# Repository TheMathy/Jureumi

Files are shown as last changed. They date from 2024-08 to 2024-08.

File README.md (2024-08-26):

# Jureumi

Jureumi is a maze-solving robot built by **Mathias Suroviak**, **Lucia Hutirová** and **Lucia Eliška Grajciarová**. He was built as our [SOČ](https://siov.sk/sutaze/stredoskolska-odborna-cinnost/) project and to attend the [Micromouse](https://en.wikipedia.org/wiki/Micromouse) competition.

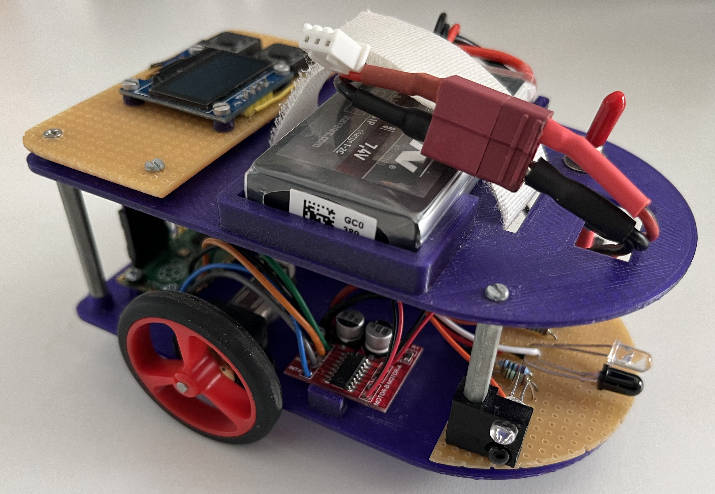
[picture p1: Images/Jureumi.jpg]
SideTop Render of Jureumi


***

## Features
Although Jureumi is relatively simple in compare with other Micromouse robots, he contains all the necessary features to solve mazes:
- Drive through the maze using two brushed DC motors
- Detect obstacles - maze walls with custom made IR distance sensors
- Scan mazes, where all walls are connected, using [Right-hand rule](https://en.wikipedia.org/wiki/Maze-solving_algorithm#Hand_On_Wall_Rule)
- Save map of the maze to raspberry pi pico flash memory

***

## Components

| Component | Model | Quantity |
| --- | --- | --- |
| Microcontroller | [Raspberry Pi Pico](https://www.raspberrypi.com/products/raspberry-pi-pico/) | 1 |
| Linear Regulator | LM317 Module | 1 |
| Motor | [Pololu 75:1 Gearmotor HP](https://www.pololu.com/product/2215) | 2 |
| Encoder | [Pololu Encoder 12 CPR](https://www.pololu.com/product/4761)| 2 |
| Wheel | [Pololu WHEEL 40×7MM - RED](https://www.pololu.com/product/1453) | 2 |
| Motor Driver | MX1508 Module | 1 |
| Ball Caster | [Pololu Ball Caster - 3/8″ Metal Ball](https://www.pololu.com/product/951) | 1 |
| IR LED | LL-503IRC2V-2AD | 3 |
| Phototransistor | BPV11F | 3 |
| Display | SSD-1306 OLED display | 1 |
| Battery | KAVAN Li-Po 350mAh/7,4V | 1 |

***

## Future improvements:
- More reliable distance sensors (sunlight cover, smaller detection angle, smaller light frequency range, ...)
- Advanced maze-solving algorithms (A*, Floodfill)
- Custom PCB including MCU
- Replace the linear voltage regulator with a buck converter

***

## Images
### Renders

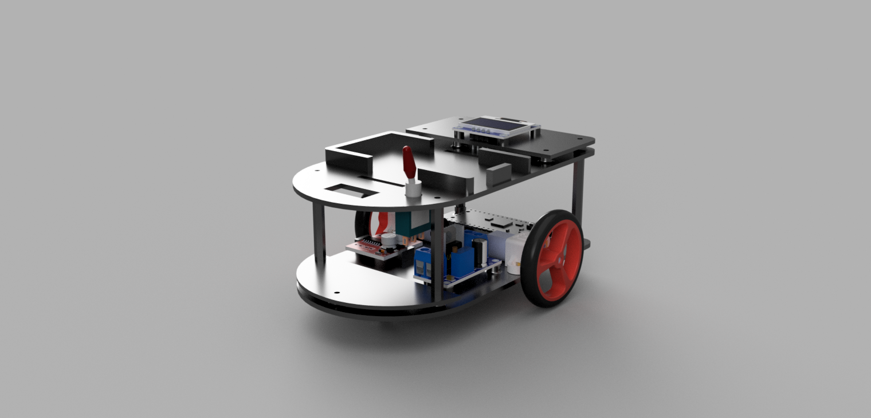
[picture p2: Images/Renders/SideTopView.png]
SideTop View Render of Jureumi

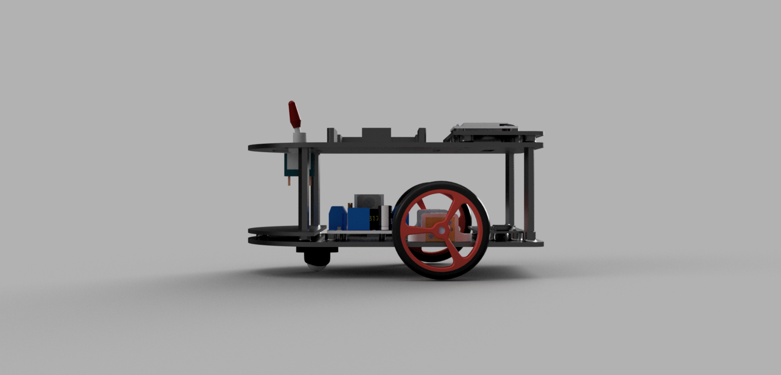
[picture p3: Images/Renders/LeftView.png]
Left View Render of Jureumi


### Visualized maze-map from robot's memory
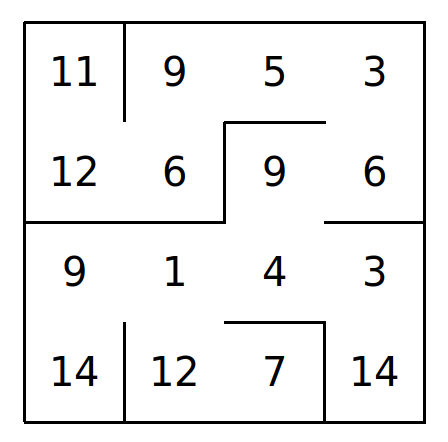
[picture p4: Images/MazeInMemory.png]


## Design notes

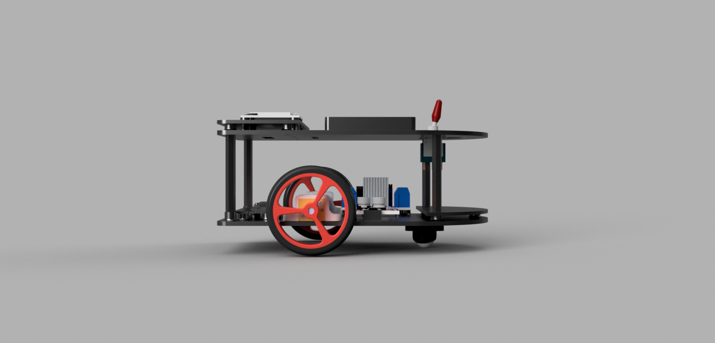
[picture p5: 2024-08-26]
Images/Renders/RightView.png

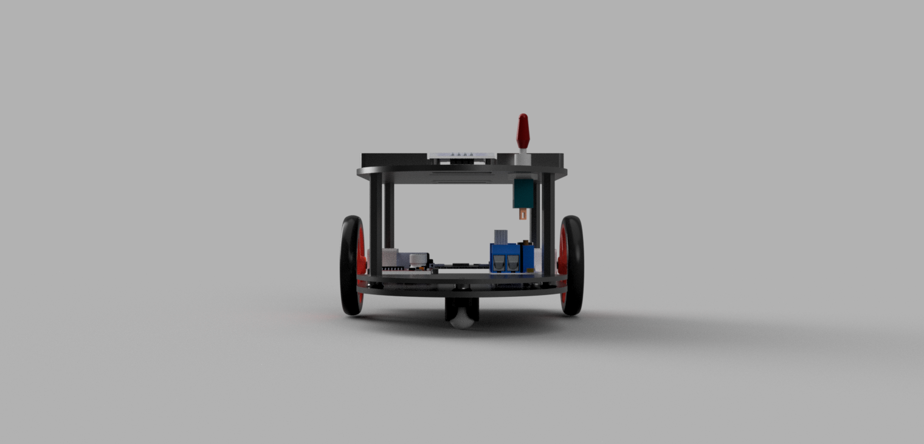
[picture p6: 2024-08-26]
Images/Renders/FrontView.png

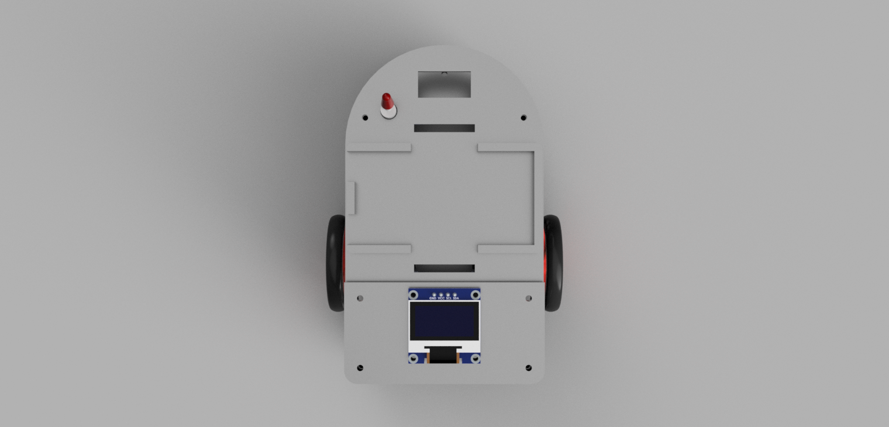
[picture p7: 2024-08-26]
Images/Renders/TopView.png

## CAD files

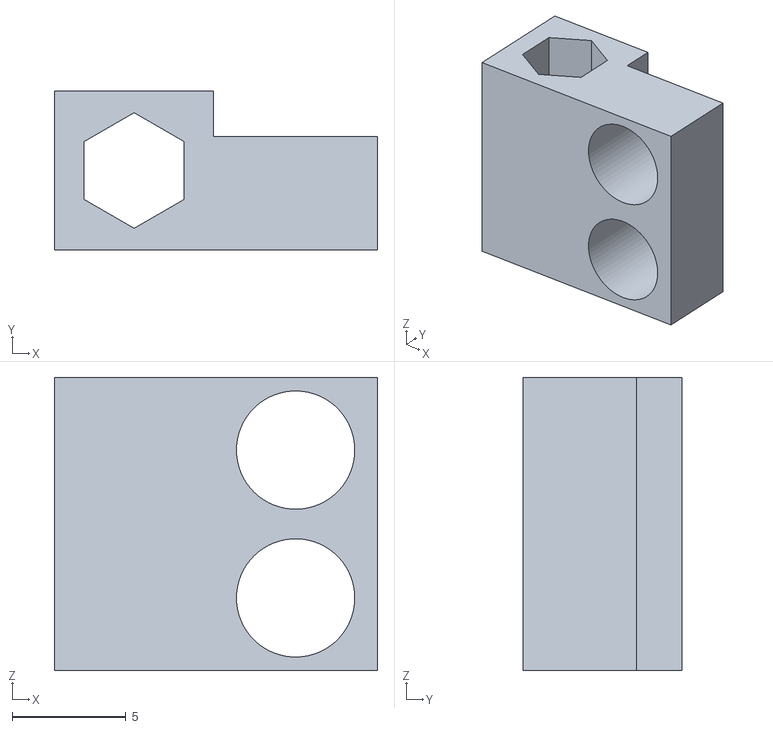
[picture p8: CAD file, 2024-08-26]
3DModels/IRSensorShield.stl
14.2 x 7.00 x 12.9

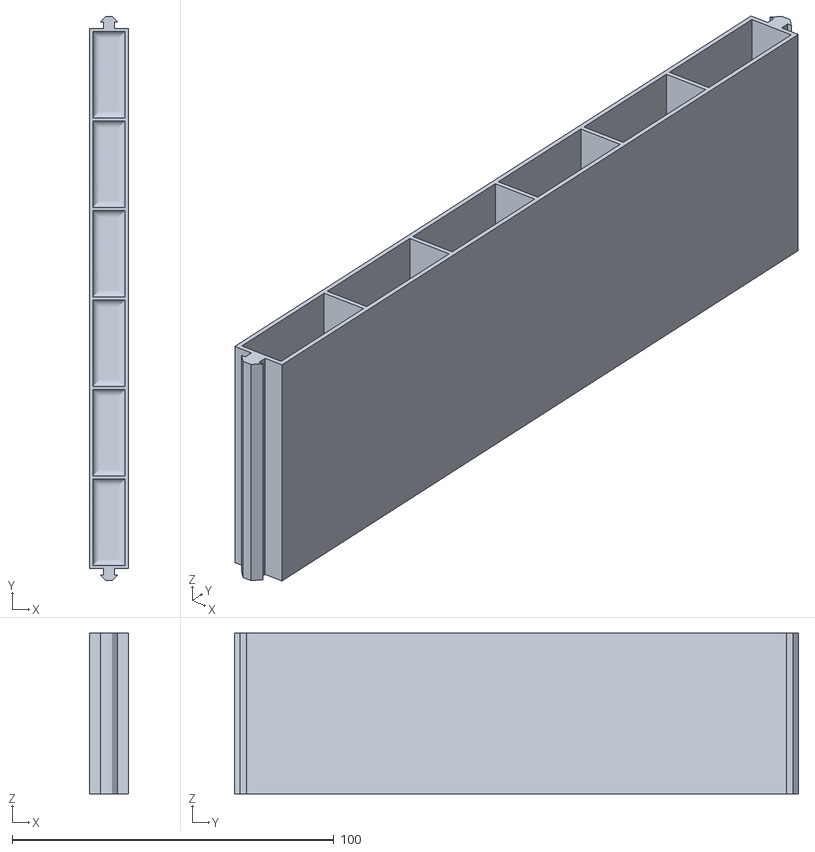
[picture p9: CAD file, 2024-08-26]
3DModels/Maze/Wall.stl
12.0 x 175.4 x 50.0

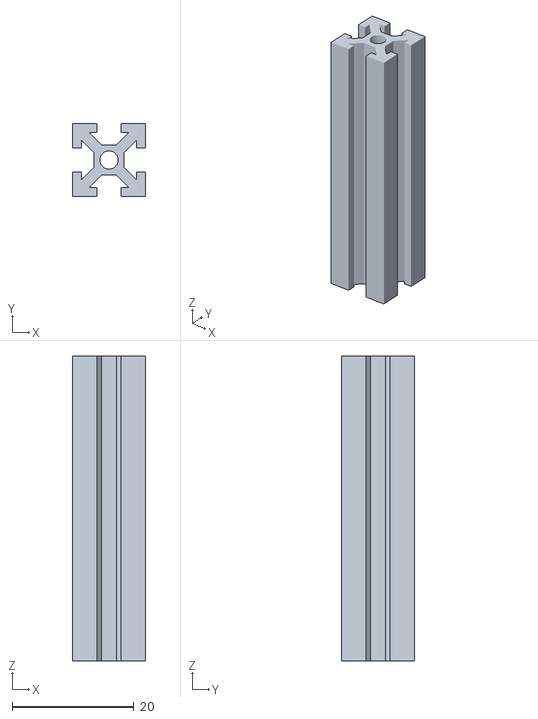
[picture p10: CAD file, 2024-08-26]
3DModels/Maze/Pole.stl
12.0 x 12.0 x 50.0

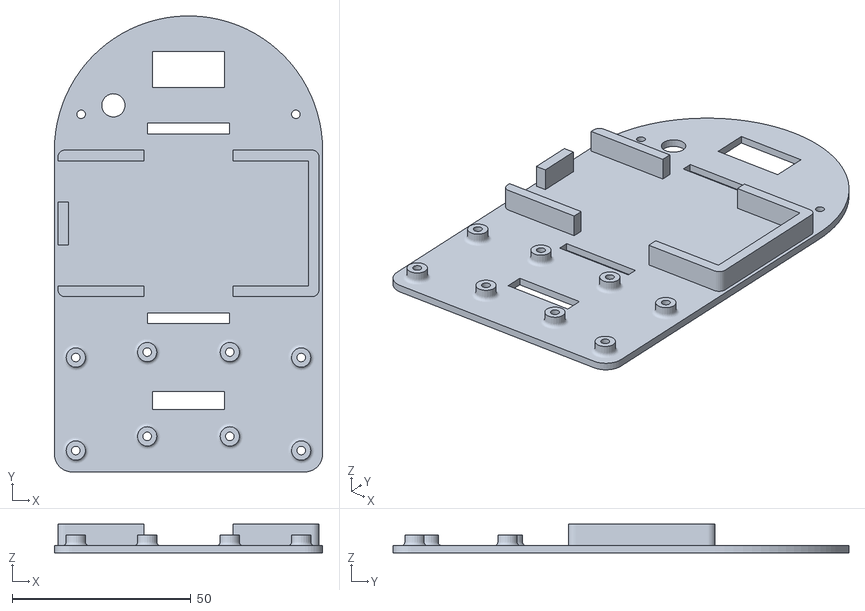
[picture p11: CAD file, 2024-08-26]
3DModels/TopBoard.stl
75.0 x 127.5 x 8.00

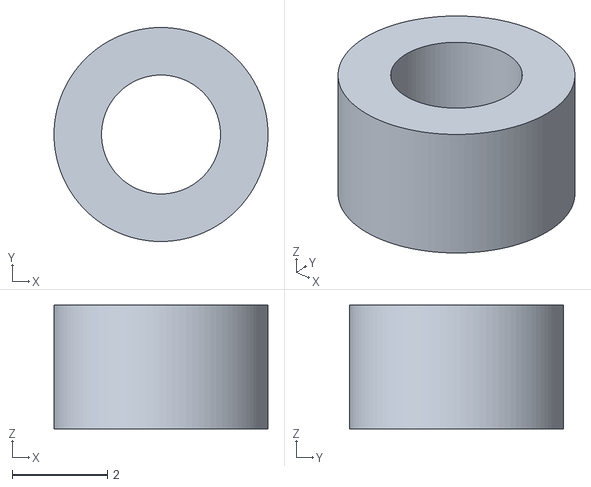
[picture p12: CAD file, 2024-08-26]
3DModels/SpacerM2x2.6.stl
4.50 x 4.50 x 2.60

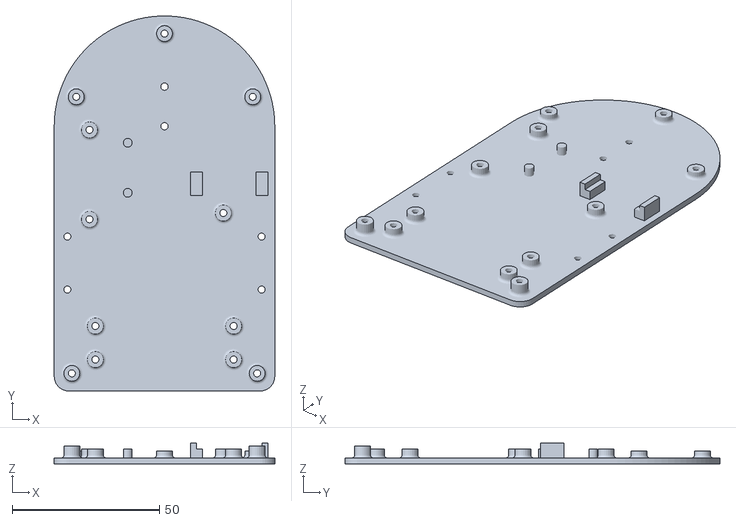
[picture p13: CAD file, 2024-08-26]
3DModels/BottomBoard.stl
75.0 x 127.5 x 7.00

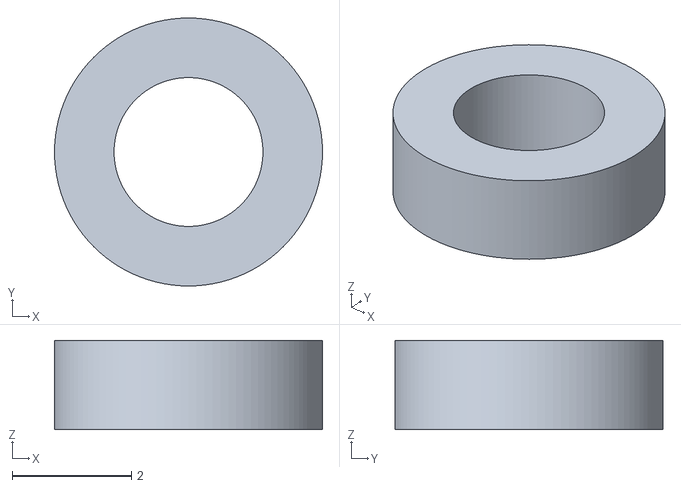
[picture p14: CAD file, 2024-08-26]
3DModels/WasherM2x1.5.stl
4.50 x 4.50 x 1.50

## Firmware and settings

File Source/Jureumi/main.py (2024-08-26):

# Main program for raspberry Pi Pico

from machine import Pin, PWM, ADC, I2C
from ssd1306 import SSD1306_I2C

import math
import time


# CONST
GEAR_RATIO = 75
PULSES_PER_REVOLUTION = 6
WHEEL_DIAMETER = 40

CELL_DISTANCE = 180

# THRESHOLDS
LEFT_TURN_THR = 45000
RIGHT_TURN_THR = 45000
FORWARD_TURN_THR = 30000

SPEED = 12000
ROTATE_SPEED = 5000

# MAZE
MAZE_SIZE = 6
MAZE_START_X = 4
MAZE_START_Y = 0

led = Pin(25, Pin.OUT)
led.on()

# Init motor pins
motor1A = PWM(Pin(16))
motor1B = PWM(Pin(17))

motor1A.freq(1000)
motor1B.freq(1000)
              
motor2A = PWM(Pin(18))
motor2B = PWM(Pin(19))

motor2A.freq(1000)
motor2B.freq(1000)
              

# Init LEDS
rightLed = ADC(Pin(26))
rightLedValue = rightLed.read_u16()
middleLed = ADC(Pin(27))
middleLedValue = middleLed.read_u16()
leftLed = ADC(Pin(28))
leftLedValue = leftLed.read_u16()

i2c = I2C(0, scl = Pin(13), sda = Pin(12), freq=400000)
time.sleep(1)
display = SSD1306_I2C(128, 64, i2c)

button = Pin(10, Pin.IN, Pin.PULL_UP)

mode = 0

def RotateSquare(squareID: int):
    if squareID > 7:
        squareID = squareID << 1
        squareID -= 16
        squareID += 1
    else:
        squareID = squareID << 1

    return squareID


class Encoder():
    def __init__(self, pinID: int) -> None:
        self._encoderPin = Pin(pinID, Pin.IN, Pin.PULL_DOWN)

        self._count = 0
        self._lastState = self._encoderPin.value()

    def Update(self) -> None:
        state = self._encoderPin.value()

        if state != self._lastState:
            self._count += 1
            self._lastState = state

    def GetRevolutionCount(self) -> float:
        return self._count / (GEAR_RATIO * PULSES_PER_REVOLUTION)
    
    def ResetCounter(self):
        self._count = 0

def SetMotorSpeeds(leftSpeed: int, rightSpeed: int) -> None:
    if rightSpeed < 0:
        motor1A.duty_u16(2 ** 16 - 1 + rightSpeed)
        motor1B.duty_u16(2 ** 16 - 1)
    else:
        motor1A.duty_u16(2 ** 16 - 1)
        motor1B.duty_u16(2 ** 16 - 1 - rightSpeed)
    
    if leftSpeed < 0:
        motor2A.duty_u16(2 ** 16 - 1 + leftSpeed)
        motor2B.duty_u16(2 ** 16 - 1)
    else:
        motor2A.duty_u16(2 ** 16 - 1)
        motor2B.duty_u16(2 ** 16 - 1 - leftSpeed)    
       
    
# Init encoders
leftEncoder: Encoder = Encoder(6)
rightEncoder: Encoder = Encoder(8)


def MoveDistance(targetDistance: float, speed: int) -> None:
    startLeftRevolutions = leftEncoder.GetRevolutionCount()
    startRightRevolutions = rightEncoder.GetRevolutionCount()

    while leftEncoder.GetRevolutionCount() - startLeftRevolutions < abs(targetDistance):
        leftEncoder.Update()
        rightEncoder.Update()

        delta = (rightEncoder.GetRevolutionCount() - startRightRevolutions) - (leftEncoder.GetRevolutionCount() - startLeftRevolutions)
        SetMotorSpeeds(int(speed - delta * 30000), int(speed + delta * 30000))

    SetMotorSpeeds(0, 0)

def RotateDistance(targetDistance: float, speed: int, leftRight: float) -> None:
    startLeftRevolutions = leftEncoder.GetRevolutionCount()
    startRightRevolutions = rightEncoder.GetRevolutionCount()

    SetMotorSpeeds(int(speed - speed * leftRight), int(-speed - speed * leftRight))
    while leftEncoder.GetRevolutionCount() - startLeftRevolutions < abs(targetDistance) and rightEncoder.GetRevolutionCount() - startRightRevolutions < abs(targetDistance):
        leftEncoder.Update()
        rightEncoder.Update()

    SetMotorSpeeds(0, 0)


# Calibrate wall distances
targetLeftValue = leftLed.read_u16()
targetRightValue = rightLed.read_u16()

direction = 1

x = MAZE_START_X + 1
y = MAZE_START_Y

mazeFile = open("maze.txt", "w")
logFile = open("log.txt", "w")

targetDistance = CELL_DISTANCE / (WHEEL_DIAMETER * math.pi)

lastLeftRevolutions = leftEncoder.GetRevolutionCount()
lastRightRevolutions = rightEncoder.GetRevolutionCount()

mazeMap = [-1] * (MAZE_SIZE ** 2)

lastButton = button.value()

while True:
    buttonValue = button.value()

    if buttonValue != lastButton:
        lastButton = buttonValue

        if buttonValue == 0:
            print("YAAY")
            mode = 1 - mode

            # Calibrate wall distances
            targetLeftValue = leftLed.read_u16()
            targetRightValue = rightLed.read_u16()

            time.sleep(1)
        

    if mode == 0:
        SetMotorSpeeds(0, 0)

        rightLedValue = rightLed.read_u16()
        middleLedValue = middleLed.read_u16()
        leftLedValue = leftLed.read_u16()

        display.fill(0)
        display.text("r: " + str(rightLedValue) + "/" + str(RIGHT_TURN_THR), 0, 35)
        display.text("m: " + str(middleLedValue) + "/" + str(FORWARD_TURN_THR), 0, 45)
        display.text("l: " + str(leftLedValue) + "/" + str(LEFT_TURN_THR), 0, 55)

        display.show()

    elif mode == 1:
        # Read encoders values
        leftEncoder.Update()
        rightEncoder.Update()

        leftRevolutions = leftEncoder.GetRevolutionCount()
        rightRevolutions = rightEncoder.GetRevolutionCount()
        
        delta = (rightRevolutions - lastRightRevolutions) - (leftRevolutions - lastLeftRevolutions)

        # Read LED values

        rightLedValue = rightLed.read_u16()
        middleLedValue = middleLed.read_u16()
        leftLedValue = leftLed.read_u16()

        deltaLed = (rightLedValue - targetRightValue) - (leftLedValue - targetLeftValue)

        deltaLed = min(deltaLed, 6000)
        deltaLed = max(deltaLed, -6000)

        delta = min(delta, 0.2)
        delta = max(delta, -0.2)

        if leftRevolutions - lastLeftRevolutions > targetDistance or middleLedValue < 20000:
            # Evaluate intersection

            SetMotorSpeeds(0, 0)

            leftTurn = leftLedValue > LEFT_TURN_THR
            rightTurn = rightLedValue > RIGHT_TURN_THR
            forwardTurn = middleLedValue > FORWARD_TURN_THR
                
            # Calculate maze squere ID and store to maze map
            if 0 <= x <= MAZE_SIZE - 1 and 0 <= y <= MAZE_SIZE - 1:
                if mazeMap[(MAZE_SIZE - y - 1) * MAZE_SIZE + x] == -1:
                    cell = 0

                    if not forwardTurn:
                        cell += 1

                    if not rightTurn:
                        cell += 2

                    if not leftTurn:
                        cell += 8

                    for i in range(direction % 4):
                        cell = RotateSquare(cell)

                    mazeMap[(MAZE_SIZE - y - 1) * MAZE_SIZE + x] = cell

            #while button.value():
                #pass

            # Right hand rule
            if rightTurn:
                direction += 1

                MoveDistance(0.1, -SPEED)
                RotateDistance(0.50 * 2, ROTATE_SPEED, -1)

                targetDistance = CELL_DISTANCE / (WHEEL_DIAMETER * math.pi) - 0.55

            elif forwardTurn:
                targetDistance = CELL_DISTANCE / (WHEEL_DIAMETER * math.pi)

            elif leftTurn:
                direction -= 1

                MoveDistance(0.1, -SPEED)
                RotateDistance(0.50 * 2, -ROTATE_SPEED, 1)

                targetDistance = CELL_DISTANCE / (WHEEL_DIAMETER * math.pi) - 0.55

            else:
                direction += 2

                RotateDistance(0.53 * 2, SPEED, 0.12)
                
                targetDistance = CELL_DISTANCE / (WHEEL_DIAMETER * math.pi) - 0.55
        

            # Calculate new coordinates
            if x == 4 and y == 0:
                SetMotorSpeeds(0, 0)
                break

            if direction % 4 == 0:
                y += 1
            elif direction % 4 == 1:
                x += 1
            elif direction % 4 == 2:
                y -= 1
            elif direction % 4 == 3:
                x -= 1

            SetMotorSpeeds(0, 0)

            lastLeftRevolutions = leftEncoder.GetRevolutionCount()
            lastRightRevolutions = rightEncoder.GetRevolutionCount()

        # Check for wall situation
        if rightLedValue <= RIGHT_TURN_THR - 2000 and leftLedValue <= LEFT_TURN_THR - 2000:    
            SetMotorSpeeds(int(SPEED + deltaLed / 1.4), int(SPEED - deltaLed / 1.4))
        elif rightLedValue <= RIGHT_TURN_THR - 2000:
            rightDelta = rightLedValue - targetRightValue
            rightDelta = min(rightDelta, 6000)
            rightDelta = max(rightDelta, -6000)

            sign = 1
            if rightDelta < 0:
                sign = -1

            SetMotorSpeeds(int(SPEED + abs(rightDelta) ** (1 / 2) * 60 * sign), int(SPEED - abs(rightDelta) ** (1 / 2) * 60 * sign))
        elif leftLedValue <= LEFT_TURN_THR - 2000:
            leftDelta = leftLedValue - targetLeftValue
            leftDelta = min(leftDelta, 6000)
            leftDelta = max(leftDelta, -6000)

            sign = 1
            if leftDelta < 0:
                sign = -1

            SetMotorSpeeds(int(SPEED - abs(leftDelta) ** (1 / 2) * 60 * sign), int(SPEED + abs(leftDelta) ** (1 / 2) * 60 * sign))

        else:
            SetMotorSpeeds(int(SPEED + delta * 60000), int(SPEED - delta * 60000)) 


for i in range(MAZE_SIZE):
    for j in range(MAZE_SIZE):
        mazeFile.write(str(mazeMap[MAZE_SIZE * i + j]) + " ")

    mazeFile.write("\n")

logFile.write("Total distance left wheel: {} mm, Total distance right wheel: {} mm\n".format(leftEncoder.GetRevolutionCount() * (WHEEL_DIAMETER * math.pi), rightEncoder.GetRevolutionCount() * (WHEEL_DIAMETER * math.pi)))


display.fill(0)

xOffset = 64 - 18
yOffset = 18
size = 6

for i in range(6):
    for j in range(6):
        code = mazeMap[MAZE_SIZE * i + j]

        if code == -1:
            continue

        if code & 1:
            display.line(xOffset + j * size, yOffset + i * size, xOffset + (j + 1) * size, yOffset + i * size, 1)

        if code & 2:
            display.line(xOffset + (j + 1) * size, yOffset + i * size, xOffset + (j + 1) * size, yOffset + (i + 1) * size, 1)
            
        if code & 4:
            display.line(xOffset + j * size, yOffset + (i + 1) * size, xOffset + (j + 1) * size, yOffset + (i + 1) * size, 1)

        if code & 8:
            display.line(xOffset + j * size, yOffset + i * size, xOffset + j * size, yOffset + (i + 1) * size, 1)

        #display.rect(xOffset + j * size, yOffset + i * size, size, size, 1)



finishX = -1
finishY = -1

for i in range(MAZE_SIZE - 1):
    for j in range(MAZE_SIZE - 1):
        UpLeft = mazeMap[MAZE_SIZE * i + j]
        UpRight = mazeMap[MAZE_SIZE * i + j + 1]
        DownLeft = mazeMap[MAZE_SIZE * (i + 1) + j]
        DownRight = mazeMap[MAZE_SIZE * (i + 1) + j + 1]

        count = 0

        if UpLeft & 2 or UpLeft & 4:
            count += 1

        if UpRight & 4 or UpRight & 8:
            count += 1

        if DownLeft & 1 or DownLeft & 2:
            count += 1

        if DownRight & 1 or DownRight & 8:
            count += 1
    
        if count == 0:
            finishX = j
            finishY = MAZE_SIZE - 1 - i

display.text("{}, {}".format(finishX, finishY), 0, 55)
print(finishX, finishY)


display.show()


led.off()
mazeFile.close()
logFile.close()
